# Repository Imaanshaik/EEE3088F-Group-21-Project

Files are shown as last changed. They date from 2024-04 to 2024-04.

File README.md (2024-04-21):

# EEE3088F-Group-21-Project

Micro-mouse Sensing and Power Modules
Welcome to the GitHub repository for the Sensing and Power Modules of the Micro-mouse project. This repository contains the design files, documentation, and code related to the development of the sensor and power subsystems for the Micro-mouse robot.

Repository Contents:
Sensing Module:

Schematics
PCB design files
Bill of Materials (BOM)
Code for sensor data processing
Power Module:

Power circuit schematics
PCB layout files
Power management code
Documentation:

Interim Design Report
Final Report
README file
Getting Started:
To get started with the project, follow these steps:

Clone the repository to your local machine:

git clone (https://github.com/Imaanshaik/EEE3088F-Group-21-Project)
Navigate to the respective folders for the Sensing and Power Modules to access the design files and documentation.

Review the README files within each module for specific instructions on setup and usage.

Contributing:
If you would like to contribute to the development of the Sensing and Power Modules, please follow these guidelines:

Fork the repository to your GitHub account.
Create a new branch for your feature or bug fix:
git checkout -b feature/new-feature
Make your changes and commit them with descriptive messages:
git commit -m "Add new sensor calibration code"
Push your changes to your fork:
git push origin feature/new-feature
Open a pull request to merge your changes into the main repository.
Contact:
For any questions or feedback regarding the Sensing and Power Modules, please contact us at [mxxsaf002@myuct.ac.za (sensing module) and shkima005@myuct.ac.za (power module)].

We look forward to collaborating with you on this exciting project!

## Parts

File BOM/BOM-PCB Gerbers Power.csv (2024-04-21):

Comment | Designator | Footprint | LCSC
MS-22D28-G020 | S1 | MS22D28G020 switch
DRV8837 | U3 | WSON-8-1EP_2x2mm_P0.5mm_EP0.9x1.6mm
Conn_02x08_Odd_Even | J1 | PinHeader_2x08_P2.54mm_Vertical
1k | R3 | R_0805_2012Metric
Jumper_2_Open | JP4 | SolderJumper-2_P1.3mm_Open_Pad1.0x1.5mm
1k | R2 | R_0805_2012Metric
TP4056 | U4 | TP4056
2.2k | RPROG2 | R_0805_2012Metric
DRV8837 | U2 | WSON-8-1EP_2x2mm_P0.5mm_EP0.9x1.6mm
LED | RED2 | D_0805_2012Metric
10k | R5 | R_0805_2012Metric
Jumper_2_Open | JP1 | SolderJumper-2_P1.3mm_Open_Pad1.0x1.5mm
0.1uF | C2 | C_0805_2012Metric
10uF | C5 | C_0805_2012Metric
10k | R4 | R_0805_2012Metric
10uF | C6 | C_0805_2012Metric
Jumper_2_Open | JP3 | SolderJumper-2_P1.3mm_Open_Pad1.0x1.5mm
0.1uF | C1 | C_0805_2012Metric
0.1uF | C4 | C_0805_2012Metric
0.1uF | C3 | C_0805_2012Metric
Conn_02x01 | J2 | PinHeader_2x01_P2.00mm_Vertical
LED | Green2 | D_0805_2012Metric
Jumper_2_Open | JP2 | SolderJumper-2_P1.3mm_Open_Pad1.0x1.5mm
2.2k | R1 | R_0805_2012Metric

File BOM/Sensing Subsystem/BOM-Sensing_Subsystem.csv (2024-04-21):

Comment | Designator | Footprint | LCSC
BPW41N | D4,D5,D6 | SENSOR-TH_BPW41N | C142586
1M | R4,R5,R6 | 6.8kresistor | C17514
6.8k | R1,R2,R3 | 6.8kresistor | C17772
SFH 4544 | D1,D2,D3 | LED_D5.0mm_Horizontal_O3.81mm_Z15.0mm | C2900370
LMV321IDBVR | U1,U2,U3 | opamp | C7972
MMBT2222A_C8512 | Q1,Q2,Q3 | babytransistor | C8512
TestPoint | TP2 | TestPoint_THTPad_D3.0mm_Drill1.5mm
TestPoint | TP3 | TestPoint_THTPad_D3.0mm_Drill1.5mm
TestPoint | TP1 | TestPoint_THTPad_D3.0mm_Drill1.5mm
Conn_02x14_Odd_Even | J1 | PinHeader_2x14_P2.54mm_Vertical

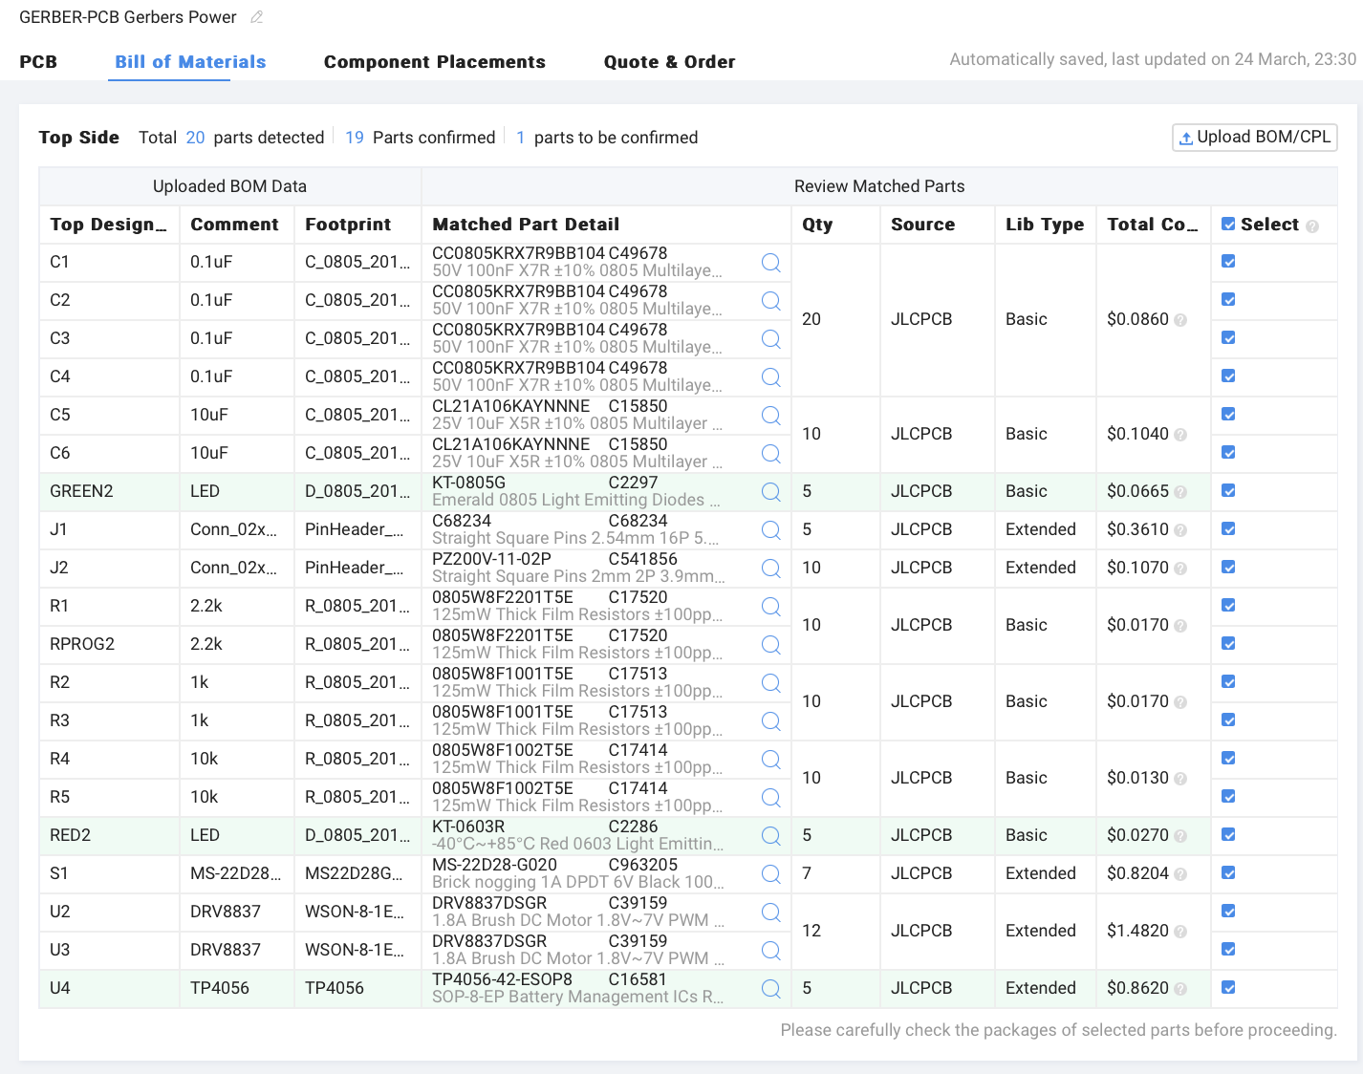
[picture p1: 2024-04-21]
BOM/EEE3088F_Project_JLCPCBBOM_SHKIMA004.png

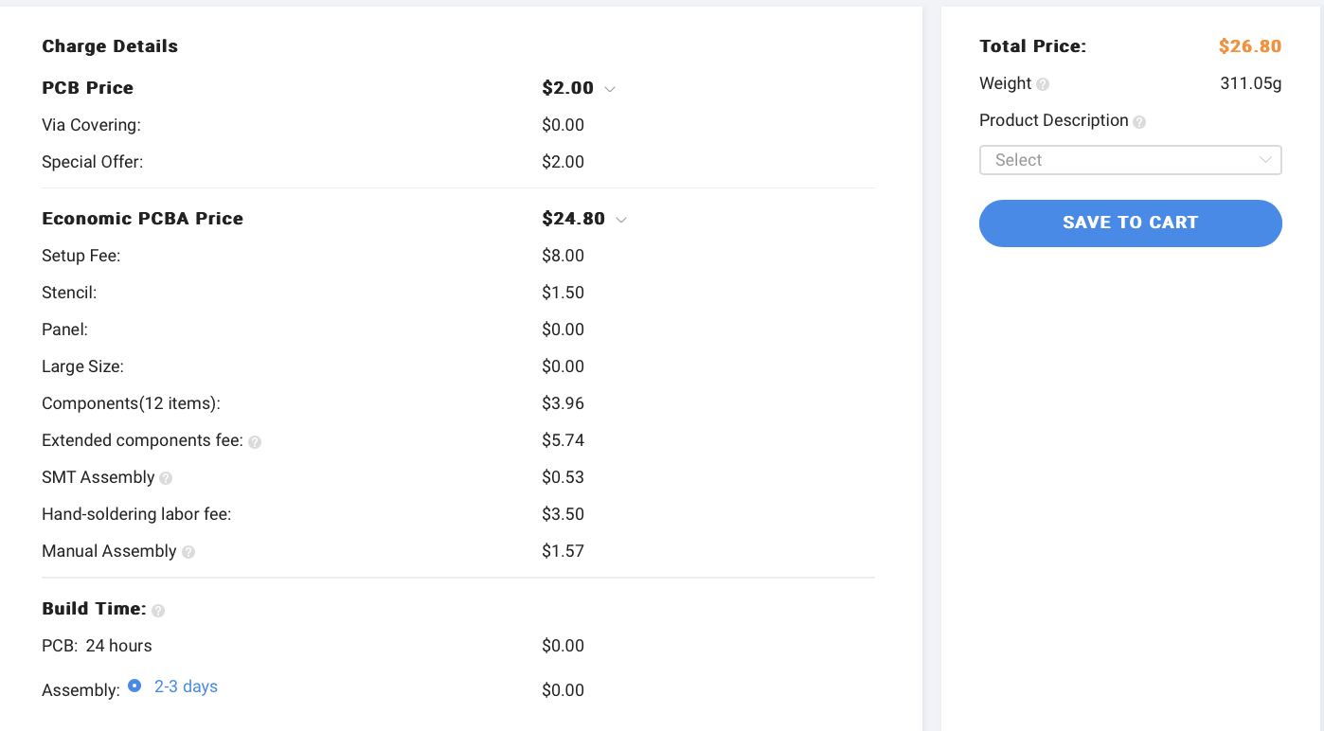
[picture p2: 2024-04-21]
BOM/EEE3088F_Project_JLCPCBacceptance_SHKIMA004.png

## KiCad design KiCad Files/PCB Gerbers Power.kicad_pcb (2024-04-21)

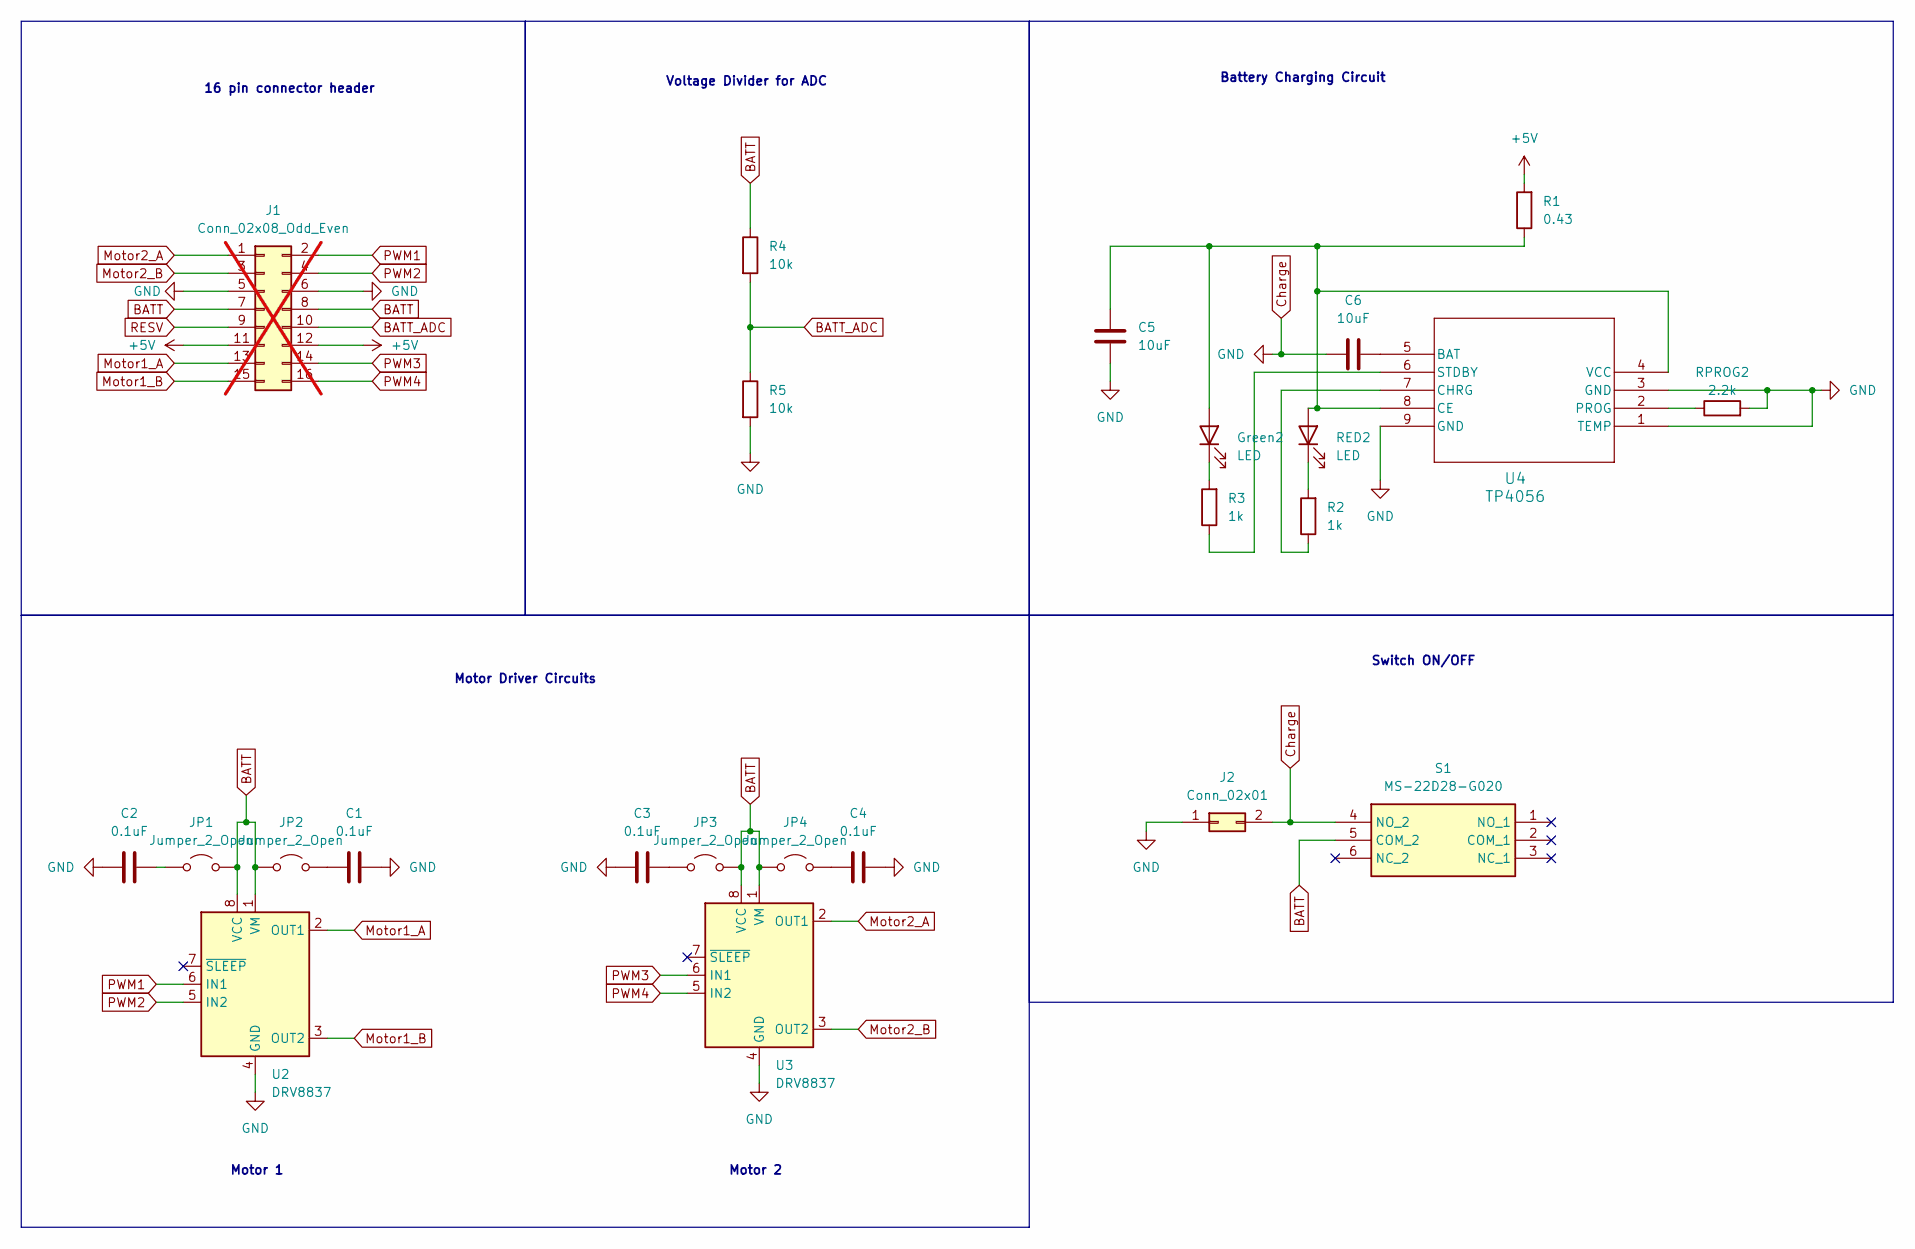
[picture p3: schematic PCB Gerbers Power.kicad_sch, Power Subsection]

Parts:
C1, C2, C3, C4: 0.1uF; C_0805_2012Metric
C5, C6: 10uF; C_0805_2012Metric
Green2: LED; D_0805_2012Metric
J1: Conn_02x08_Odd_Even; PinHeader_2x08_P2.54mm_Vertical; not fitted
J2: Conn_02x01; PinHeader_2x01_P2.00mm_Vertical
JP1, JP2, JP3, JP4: Jumper_2_Open; SolderJumper-2_P1.3mm_Open_Pad1.0x1.5mm
R1: 0.43; R_0805_2012Metric
R2, R3: 1k; R_0805_2012Metric
R4, R5: 10k; R_0805_2012Metric
RED2: LED; D_0805_2012Metric
RPROG2: 2.2k; R_0805_2012Metric
S1: MS-22D28-G020; MS22D28G020 switch; Manufacturer_Part_Number MS-22D28-G020
U2, U3: DRV8837; WSON-8-1EP_2x2mm_P0.5mm_EP0.9x1.6mm
U4: TP4056

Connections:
+5V: J1.11, J1.12, R1.2
BATT: J1.7, J1.8, JP1.2 (B), JP2.1 (A), JP3.2 (B), JP4.1 (A), R4.1, S1.5 (COM_2), U2.1 (VM), U2.8 (VCC), U3.1 (VM), U3.8 (VCC)
BATT_ADC: J1.10, R4.2, R5.1
Charge: C1.2, C2.1, C3.1, C4.2, C5.2, C6.1, J1.5, J1.6, J2.1, J2.2, R5.2, RPROG2.2, S1.4 (NO_2), U2.4 (GND), U2.9 (GND), U3.4 (GND), U3.9 (GND), U4.1 (TEMP), U4.3 (GND), U4.9 (GND)
Motor1_A: J1.13, U2.2 (OUT1)
Motor1_B: J1.15, U2.3 (OUT2)
Motor2_A: J1.1, U3.2 (OUT1)
Motor2_B: J1.3, U3.3 (OUT2)
unnamed: C5.1, Green2.2 (A), R1.1, RED2.2 (A), U4.4 (VCC), U4.8 (CE)
unnamed: Green2.1 (K), R3.2
unnamed: C2.2, JP1.1 (A)
unnamed: C1.1, JP2.2 (B)
unnamed: C3.2, JP3.1 (A)
unnamed: C4.1, JP4.2 (B)
unnamed: R2.2, RED2.1 (K)
unnamed: C6.2, U4.5 (BAT)
unnamed: R2.1, U4.7 (CHRG)
unnamed: RPROG2.1, U4.2 (PROG)
unnamed: R3.1, U4.6 (STDBY)
PWM1: J1.2, U2.6 (IN1)
PWM2: J1.4, U2.5 (IN2)
PWM3: J1.14, U3.6 (IN1)
PWM4: J1.16, U3.5 (IN2)
RESV: J1.9

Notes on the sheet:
Motor Driver Circuits
Voltage Divider for ADC
Battery Charging Circuit
16 pin connector header
Switch ON/OFF
Motor 1
Motor 2

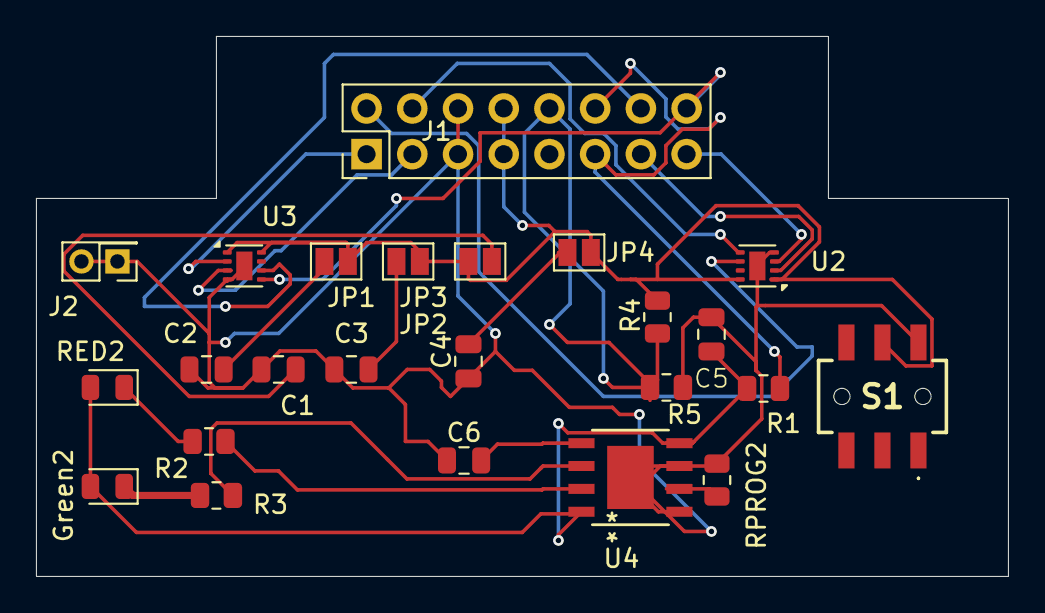
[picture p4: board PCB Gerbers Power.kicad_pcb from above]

Board: 2 copper layers, 54.0 x 30.0 mm, 24 parts (0 on the bottom side), 23 nets.

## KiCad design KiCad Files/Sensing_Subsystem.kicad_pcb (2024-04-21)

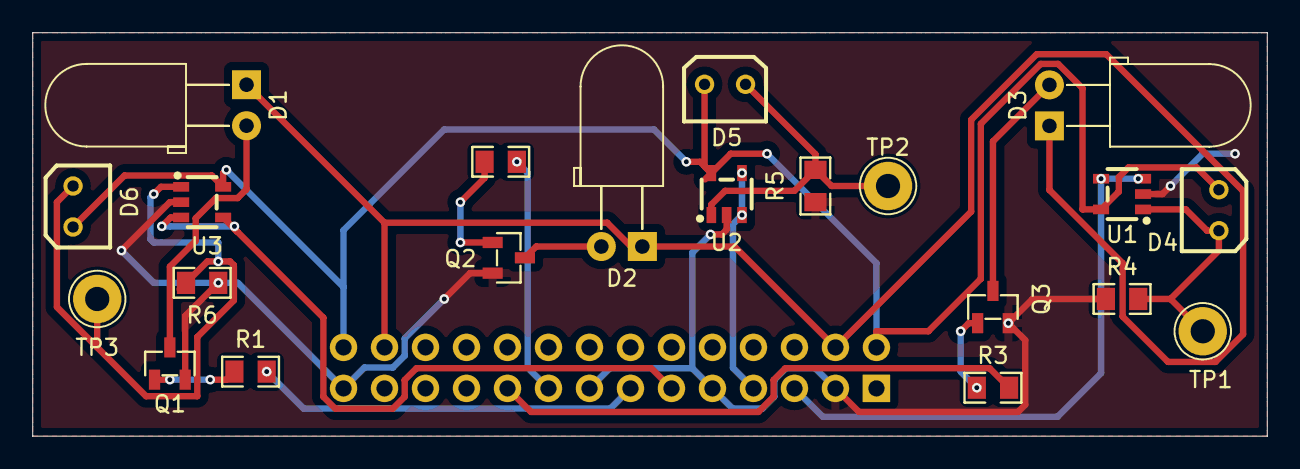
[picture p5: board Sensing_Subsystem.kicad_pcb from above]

Board: 2 copper layers, 76.5 x 25.0 mm, 22 parts (1 on the bottom side), 18 nets.

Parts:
D1, D2, D3: SFH 4544; LED_D5.0mm_Horizontal_O3.81mm_Z15.0mm
D4, D5, D6: BPW41N; SENSOR-TH_BPW41N
J1: Conn_02x14_Odd_Even; PinHeader_2x14_P2.54mm_Vertical
Q1, Q2, Q3: MMBT2222A_C8512; babytransistor
R1, R2, R3: 6.8k; 6.8kresistor
R4, R5, R6: 1M; 6.8kresistor
TP1, TP2, TP3: TestPoint; TestPoint_THTPad_D3.0mm_Drill1.5mm
U1, U2, U3: LMV321IDBVR; opamp

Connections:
+3.3V: D4.2 (C), D5.2 (C), D6.2 (C), J1.2, J1.28, U1.5 (V+), U2.5 (V+), U3.5 (V+)
BATT: D1.1 (A), D2.1 (A), D3.1 (A), J1.4, J1.26
GND: J1.3, J1.9, J1.15, J1.27, Q1.2 (E), Q2.2 (E), Q3.2 (E), R4.1, R5.1, R6.1, U1.2 (GND), U2.2 (GND), U3.2 (GND)
unnamed: D1.2 (C), Q1.3 (C)
unnamed: D2.2 (C), Q2.3 (C)
unnamed: D3.2 (C), Q3.3 (C)
unnamed: D4.1 (A), R4.2, TP1.1, U1.1 (+)
unnamed: D5.1 (A), R5.2, TP2.1, U2.1 (+)
unnamed: D6.1 (A), R6.2, TP3.1, U3.1 (+)
unnamed: Q1.1 (B), R1.2
unnamed: Q2.1 (B), R2.2
unnamed: Q3.1 (B), R3.2
PA3: J1.5, U1.3 (-), U1.4 (OUT)
PA4: J1.7, U2.3 (-), U2.4 (OUT)
PA5: J1.11, U3.3 (-), U3.4 (OUT)
PA6: J1.13, R1.1
PA7: J1.17, R2.1
PC4: J1.19, R3.1

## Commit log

2024-04-21 Create Power schematic
2024-04-21 power subsystem
2024-04-21 bill of materials
2024-04-21 Create Sensing Module Gerbers
2024-04-21 Create Sensor Module Gerbers
2024-04-21 Create Sensing Subsystem BOM
